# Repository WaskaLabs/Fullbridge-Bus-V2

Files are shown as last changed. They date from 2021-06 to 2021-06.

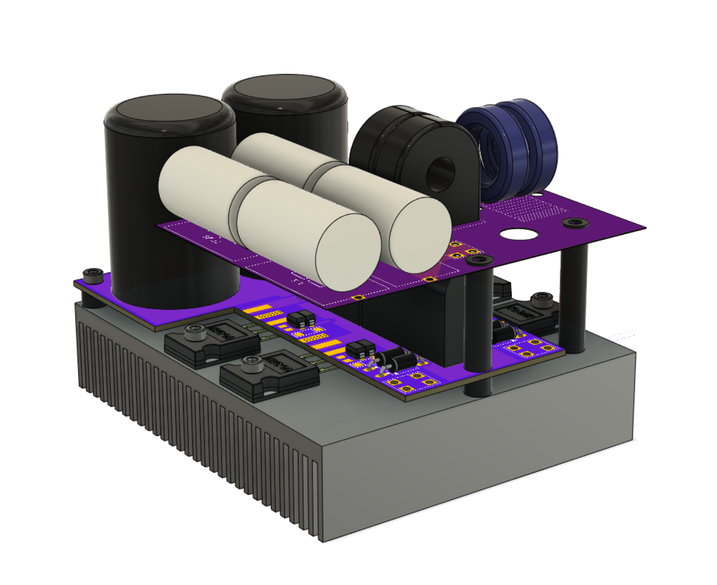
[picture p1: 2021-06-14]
PICS/3D_4.png

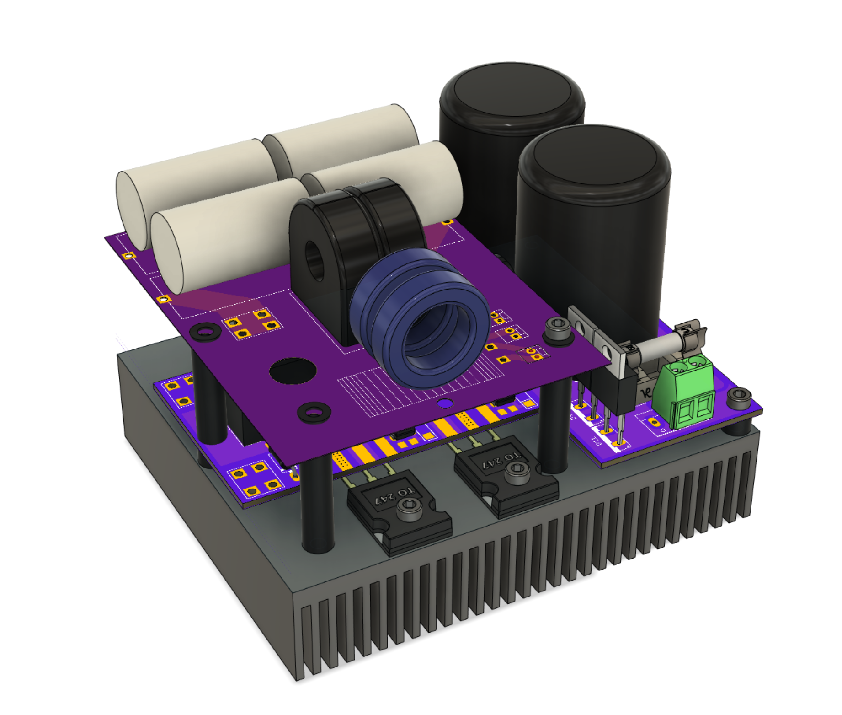
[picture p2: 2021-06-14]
PICS/3D_3.png

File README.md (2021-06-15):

# Fullbridge-Bus-V2
The full-bridge bus 2.0 is a fully integrated "high side" system designed for SSTC, DRSSTC Tesla coils, and other high power inverter applications.

PCB and Kits available for sale in the WaskaLabs store on tindie.com

Finished System Specs:

- Works with 110 and 220 AC voltages (requires relevant components for voltage!)
- High current design capable of ~300+ Apk
- Low stray inductance bridge design
- TO-247 MOSFETs or IGBTs - Surface mounted for easy and fast replacement
- Direct mount to large 100mm X 120mm heatsink for maximum temperature handling
- 10A RMS bridge rectifier and bus capacitors (voltage doubler configuration, can be set up as standard rectified) with high current input for mains AC or variac AC voltage.
- Safety circuits (6x20mm fuse (Comes with fast-blow 10A), bus capacitor bleeder resistor)
- Gate drive components (Series resistor, antiparallel switch-off diode, TVS diode) and marked solder pads for easy GDT connection.
- Snubber capacitors (0.66uF total)
- Optional diodes (freewheel or TVS on inverter output)
- High current screw connectors used (All metal)
- Optional MMC and CT board for all-in-one DRSSTC system (Coming soon)

Comes with:

- PCB
- SMD components (pre-soldered)
- Connectors (pre-soldered)
- Bridge rectifier (pre-soldered)
- Bleeder resistor (pre-soldered)
- Fuse holder and 10A fast-blow fuse (pre-soldered)
- 4x silicone heat pads
- Printed hole placement guide

Required - Not included in kit:

- Bus capacitors (~$8 each eBay, Amazon) (Choose appropriate voltage for your country)
- IGBTs or MOSFETs (Mouser, Digikey) (Spec for your specific design)
- 100x120mm Heatsink ($10 on Amazon)
- M3 screws and nylon standoffs
- GDT (DIY or available as an addon)

IGBT and MOSFET recommendations:

- FGA60N65SMD (Best in my experience) (Great for DRSSTC)
- FGA60N60SMD (Similar to 60N65) (Great for DRSSTC)
- IRFP460 (Great for higher frequency, low current SSTC designs)

Rectifier & Bus:

The voltage doubler configuration doubles the peak-to-peak voltages seen on the AC input. For example, US mains is 110V RMS, but ~170Vpp. So if US mains is connected directly to the input, it should charge the capacitor bank to 2 x 170V (~340V). The capacitors on the bus are connected in series, so each capacitor should be rated to hold the full Vpp of the mains input (in the US, I like to use 250V). It is highly advisable to spec these caps to handle >30% more than the voltage you expect to see in them, so a 500V total cap charged to 340V is a safe bet. In 220V land, you will want to use 450V capacitors for a total of 900V. Bare in mind that the total capacitance of the bus will decrease by half as the voltage doubles. So two 250V 1000uF caps in series will give you 500V at 500uF. This should be kept in consideration when designing the system.

Recommendations:

- US mains (110V RMS) - 250V 1000uF capacitors (10mm lead spacing, 35mm dia max)
- International mains (220V RMS) - 450V 680 - 1000uF capacitors (10mm lead spacing, 35mm dia max)

If you plan to modify the board to a standard rectified voltage, spec your caps accordingly. I would suggest ~100V caps for US mains (200V total rating), doubling it for 220V mains, at the highest uF you can get in the correct footprint to fit the PCB.

The KBU-1010 bridge rectifier is rated for 10A continuous and 300A surge. If you plan to run high currents monitor the temperature of the rectifier and add a heatsink if needed. The fuse is a 6x20 cylindrical type and are standard and available cheap online or locally at hardware stores. 

Inverter & Gates:

The inverter portion is pretty straightforward. The switches (IGBTs or MOSFETs) are connected directly to the heatsink with a silicone heat pad (sil pad) to electrically isolate the switches from the heatsink (Very important!). The pins of the switches should be bent upwards before mounting, then bent to contact the pads and soldered in place. Removal can be done with a soldering iron, but the simple solution is to use hot air to heat the pads. It is easier to do this after unscrewing the switches from the heatsink, otherwise you may not be able to disconnect it easily. The leads can also be clipped first if this becomes an issue.

The Gate Drive Transformer (GDT, typically 1:1:1:1:1) should be wound and phased. The secondary windings of the GDT should be soldered directly to the pads with the phase wires soldered to the pads with silkscreen around them, and the anti-phase ends soldered to the other pad. Make sure to wind the GDT with enough extra wire to make it easy to mount (I like to mount them to the side of the heatsink). One important note is that the GDT secondaries should ALL BE LENGTH MATCHED to avoid skew in the timing between the switches. 

The gate components are not one size fits all. The gates and waveforms should be thoroughly tested to assure the switching waveform is correct. If it isn't, you may need to change gate resistors and remove the diodes, etc. until you can get it right. The TVS diodes are SMAJ26 26V TVS which is designed for up to 24V drive voltages. If using lower voltages you may want to change the value of the TVS. Tuning gates is not in the scope of this document, but it is an art and takes some time to get right. But having a proper driver, GDT, gate components, and the right switches are important in getting this right. A good resource for this is Ritchie Burnett's GDT waveform troubleshooting guide.

Step by Step Assembly:

1. Spec and purchase all components for your design. Refer to BOM.
2. Solder bus caps onto PCB and test the DC voltage across the bus as well as voltage drain from bleeder resistor (recommended through a variac!).
3. Drill and tap all M3 holes in the PCB (Use printable guide). Aluminum is soft, so be careful here! If you accidentally strip the holes, you can run a longer screw all the way through and a nut on the back of the heatsink.
4. Screw down TO-247 IGBT switches with a sil pad to keep it electrically separated from the heatsink. I like to use thermal paste on both sides of the silpad for added thermal conduction. Make sure to bend the pins upwards so the PCB fits in between them.
5. Mount the PCB to the heatsink using standoffs (3 - 5mm is usually fine). Make sure the PCB connections and solder points do NOT and will NOT touch the heatsink!!
6. Bend the IGBT switch leads down to the pads and solder them in place.
7. Mount the GDT and solder the wires to the gate drive pads. Ensure correct phasing.

Testing Gates:

1. Connect a proper driver to the GDT primary and drive the gates at a frequency as close as possible to your desired operation frequency (Function generator to the GDT driver works well)
2. Test the Gates:
	1. Probe the gate drive signal to assure gate waveforms look good using an oscilloscope.
	2. Change out components or circuit elements as needed to get a good gate drive waveform. Not always needed.
	3. Assure all gates look good before proceeding...

Testing Inverter:

1. Make sure you are interrupting the output or have a high enough impedance to not drain your capacitors. This is design dependant, but should be done for any SSTC/DRSSTC design
2. Connect the load to the inverter output (Primary coil you plan to drive or high Z load for low voltage testing) (NO SECONDAY IF SSTC/DRSSTC)
3. Connect a variac and set the DC bus voltage to a low test voltage (~20-50V)
4. Hook up an oscilloscope between D/S leads on one of the switches and test the waveform. Do this with all switches. Assure they are all switching properly before proceeding.
5. Now test the output of the inverter. Be sure you are seeing a proper square wave. If you see a stair step pattern, one of the switches may be phased wrong. You may see droop in the center of the square wave depending on your load. Careful with MMCs here is using DRSSTCs. You wont be driving at resonance so this may give you a weird output. Try removing it if it causes issues.
6. Now you can increase the voltage and watch the waveforms on the scope to assure it is working as expected.

Troubleshooting:

- Make sure all gates are phased properly and being driven in the correct direction
- Test different gate drive components and values
- Make sure none of the switches are bad. Rare but it happens. If the bridge blows, all the switches may need to be replaced even if some seem okay
- Make sure you are providing enough drive current to the GDT
- Make sure your load has enough impedance to not just drain the caps too fast to see inverting voltages

This design is meant to be configurable and modular to be able to fit many topologies. There are far too many variations in application, drive methods, and use cases for me to be able to help in the debugging. If you have issues getting it to work, do your research and read up on forums. I have provided schematics and resource information on the system so that you have all information necessary to figure out the issue. But standard troubleshooting like adding/removing components and thinking through the design will be the only way to get it running. I am happy to help when I can, but ultimately what you build with this cannot be fixed IT style.

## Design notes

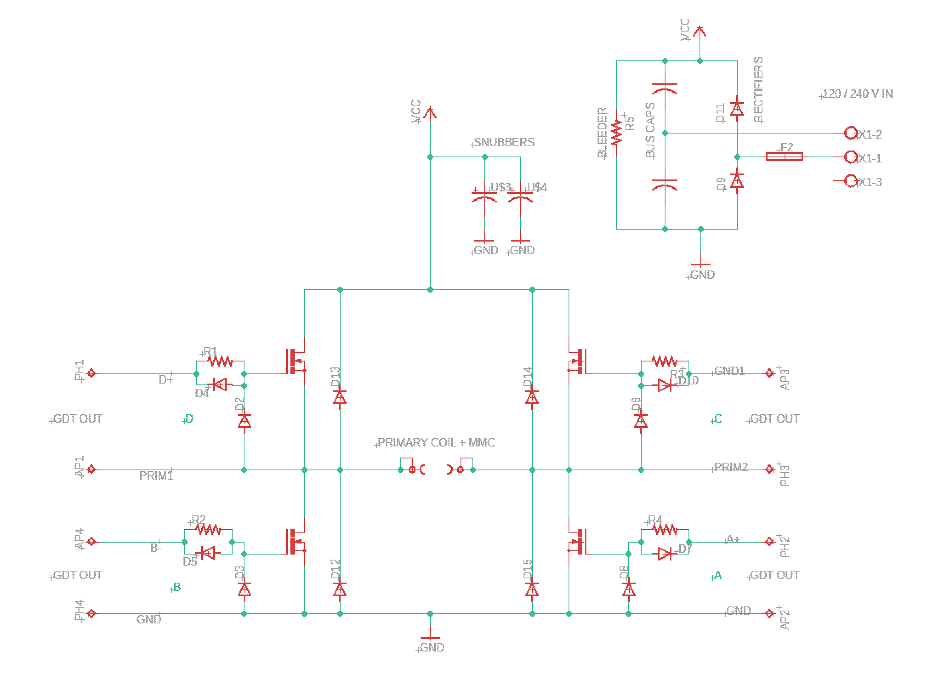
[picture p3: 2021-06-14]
PICS/SCHEMATIC.png

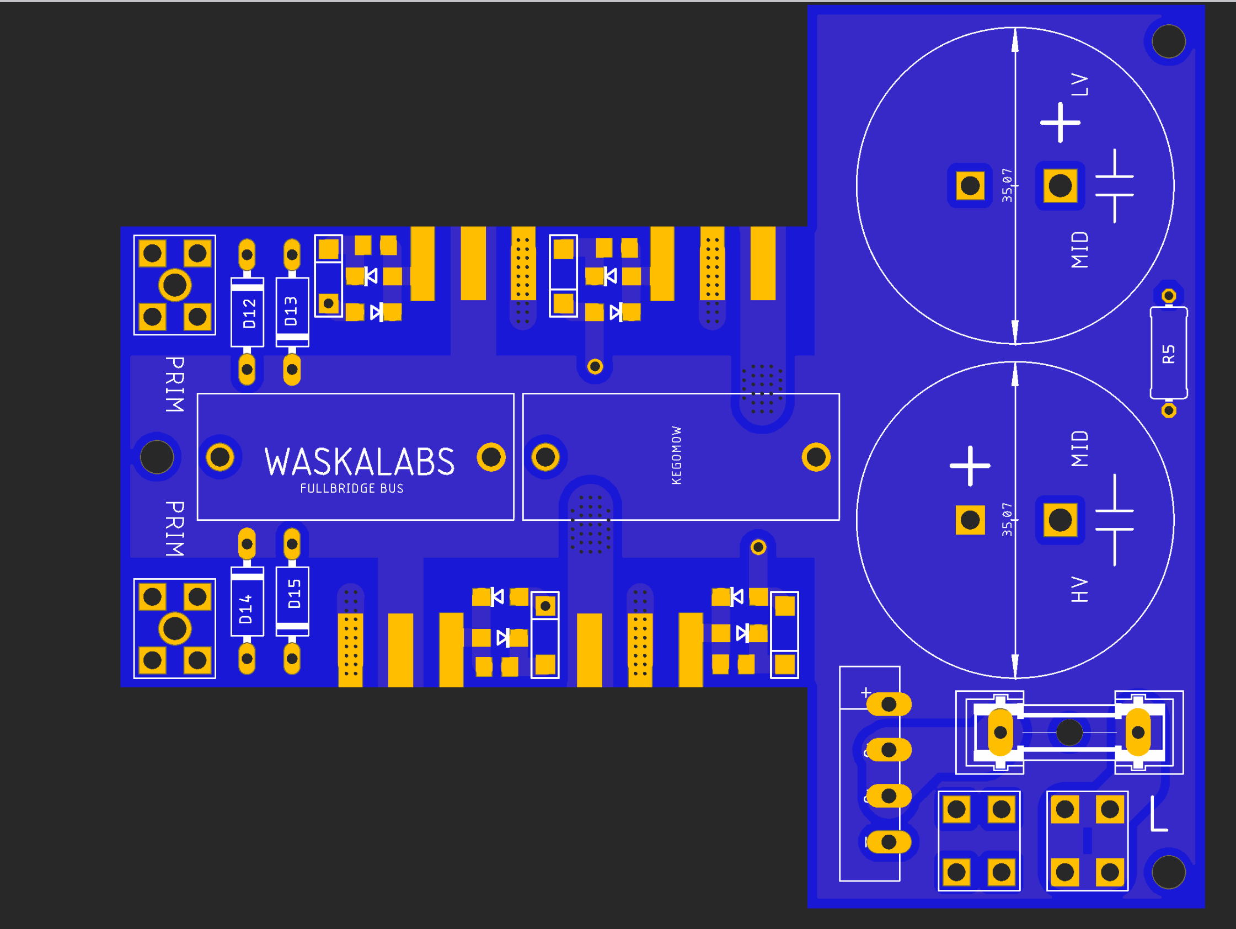
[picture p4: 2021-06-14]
PICS/PCB_TOP.png

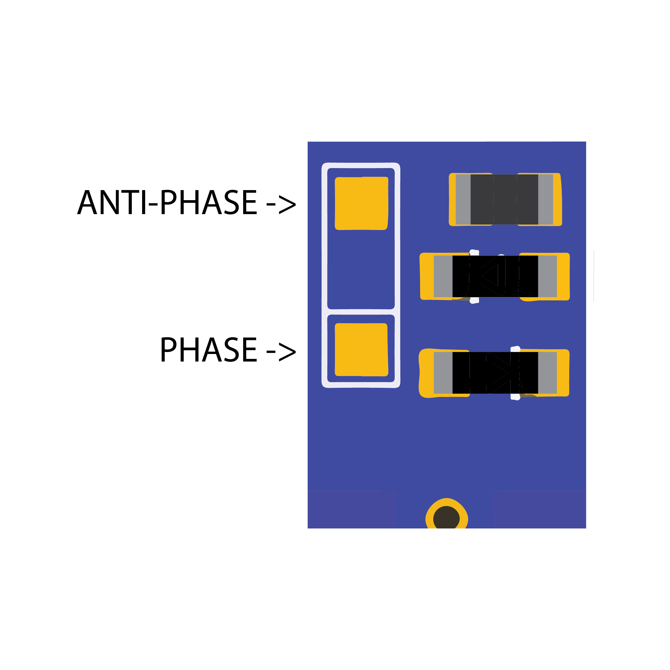
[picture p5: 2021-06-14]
PICS/PHASING.png

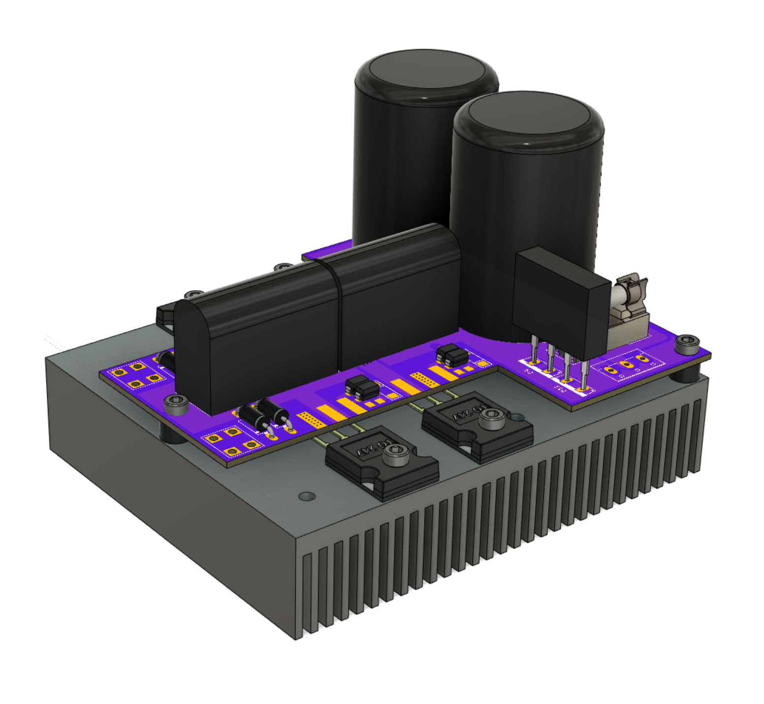
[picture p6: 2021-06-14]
PICS/3D_1.png

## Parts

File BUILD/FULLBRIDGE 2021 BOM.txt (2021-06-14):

Qty Value           Device          Package    Parts                                  Description               MF MPN         OC_FARNELL OC_NEWARK POPULARITY TP_SIGNAL_NAME

4                   R-US_M1206      M1206      R1, R2, R3, R4                         RESISTOR, American symbol                                                              

4   SMAJ26CA        DIODE-DO214AC   DO214AC    D2, D3, D6, D8                         DIODE                                                         14                       

4   SS14-E3/5AT     DIODE-DO214AC   DO214AC    D4, D5, D7, D10                        DIODE                                                         14                       

1   100K 2W         R-US_0411/12    0411/12    R5                                     RESISTOR, American symbol                                                              

1   20X5 FUSE       GSH15           GSH15      F1                                     FUSE HOLDER                  64900001039 1271673    02P0318                            

4   440V TVS        1N5060GP        DO15-12    D12, D13, D14, D15                     DIODE                                                         0                        

2   CHINEMKP        CHINEMKP        CHINESEMKP U$3, U$4                                                                                                                      

4   FGA60N65SMD_SMD FGA60N65SMD_SMD TO247BH    U$5, U$6, U$7, U$8                                                                                                            

1   KBU-1010        RECTIFIER-KBU   KBU        B2                                     Rectifier                                                     0                        

4   KEY7788         KEY7788         7788       LIVE, NEUTRAL, U$1, U$2                                                                                                       

2   VARIES	    CAPACITOR       10x35mm    BUS CAPS

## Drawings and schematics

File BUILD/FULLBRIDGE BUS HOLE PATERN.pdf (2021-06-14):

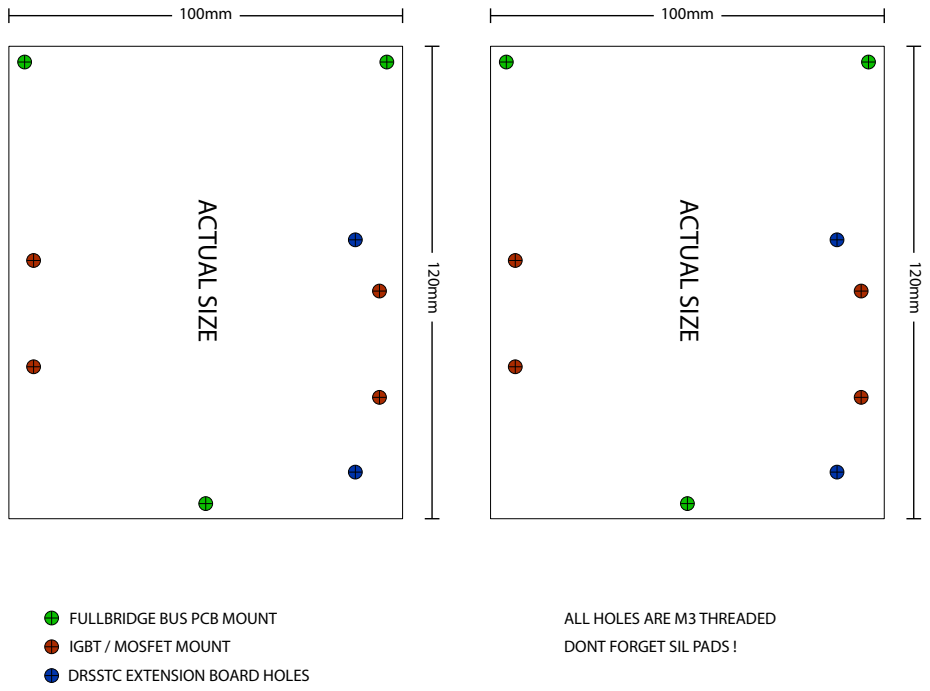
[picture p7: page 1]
ACTUAL SIZE

FULLBRIDGE BUS PCB MOUNT
IGBT / MOSFET MOUNT
DRSSTC EXTENSION BOARD HOLES

ALL HOLES ARE M3 THREADED
DONT FORGET SIL PADS !
